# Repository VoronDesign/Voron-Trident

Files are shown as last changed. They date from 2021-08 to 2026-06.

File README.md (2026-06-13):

# Voron Trident
**[CLICK HERE TO DOWNLOAD](https://voron.zip/done/VT.zip)**

The above link includes the stealthburner toolhead files which are compatible with several of the printers in the Voron lineup. 
To keep things organized, StealthBurner’s files are maintained separately. 
the Stealthburner Repository can be browsed by clicking [HERE](https://github.com/VoronDesign/Voron-Stealthburner)

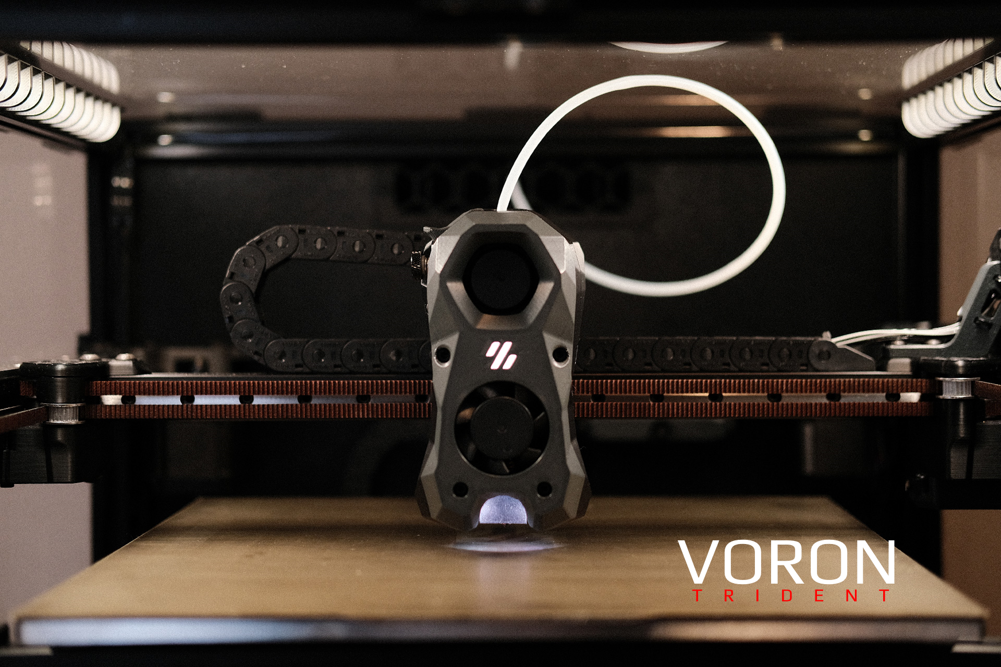
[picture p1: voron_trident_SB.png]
Image of Voron Trident


The official release of the Voron Trident 3D printer.  You can find the Bill of Materials in the configurator located at the [Voron Design]( http://vorondesign.com/voron_trident) web site.  The recommended sizes for this printer are 250x250x250, 300x300x250 and 350x350x250.

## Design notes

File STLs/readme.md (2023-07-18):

you can download the entire STL folder by clicking **[HERE](https://download-directory.github.io/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)**

This printer uses the StealthBurner toolhead, which is compatible with several of the printers in the Voron lineup. 
To keep things organized, StealthBurner’s files are maintained separately. 
the Stealthburner STL's can be downloaded by clicking **[HERE](https://download-directory.github.io/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)**

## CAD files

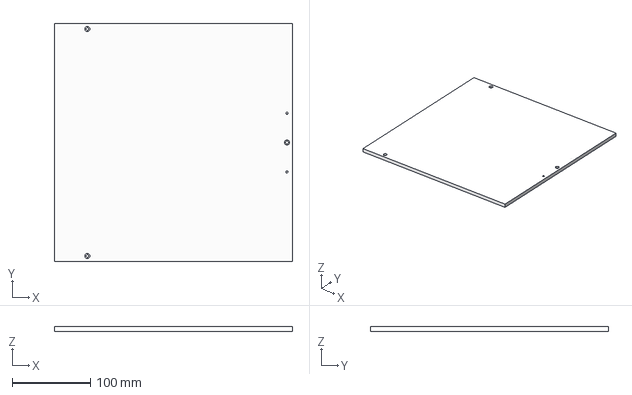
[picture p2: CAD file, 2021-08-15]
Drawings_DXFs/Build_Plate/MIC6_Bed_300.step
304.0 x 304.0 x 6.35 mm

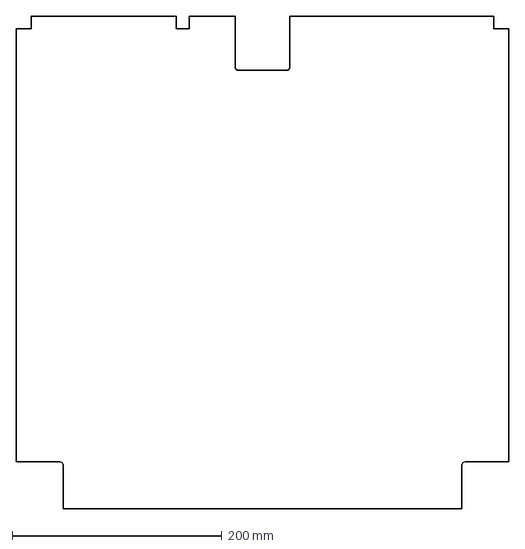
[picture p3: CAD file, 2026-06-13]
Drawings_DXFs/Panels/350_deck.dxf
469.0 x 469.0 mm

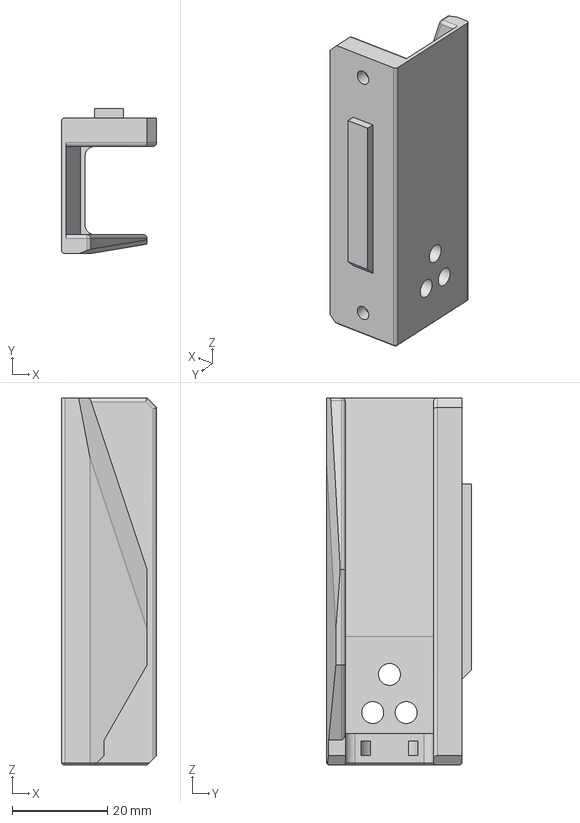
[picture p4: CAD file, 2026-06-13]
experimental/horiz_chain_umb/umbilical_mount_bottom.step
20.0 x 30.5 x 77.0 mm

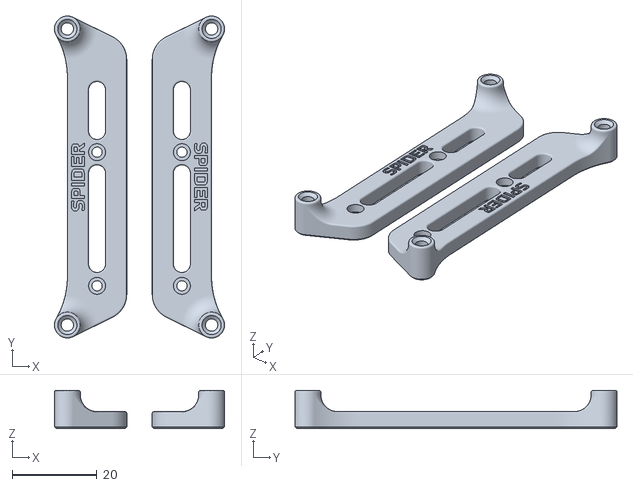
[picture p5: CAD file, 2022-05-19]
STLs/electronics_bay/controller_mounts/Spider_bracket_set.stl
40.1 x 75.9 x 9.00

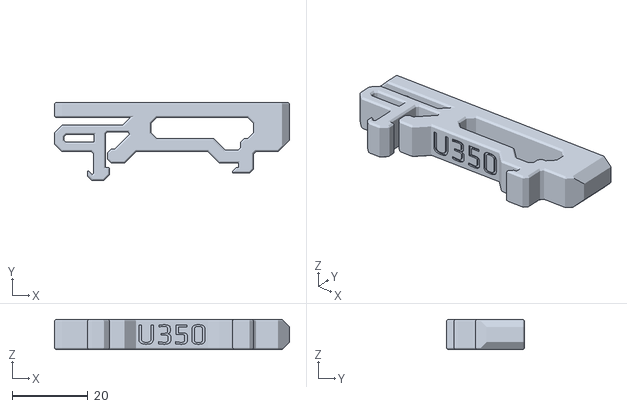
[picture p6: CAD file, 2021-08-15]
STLs/electronics_bay/other_ps_mounts/UHP_350_Mount_x2.stl
62.0 x 20.6 x 8.00

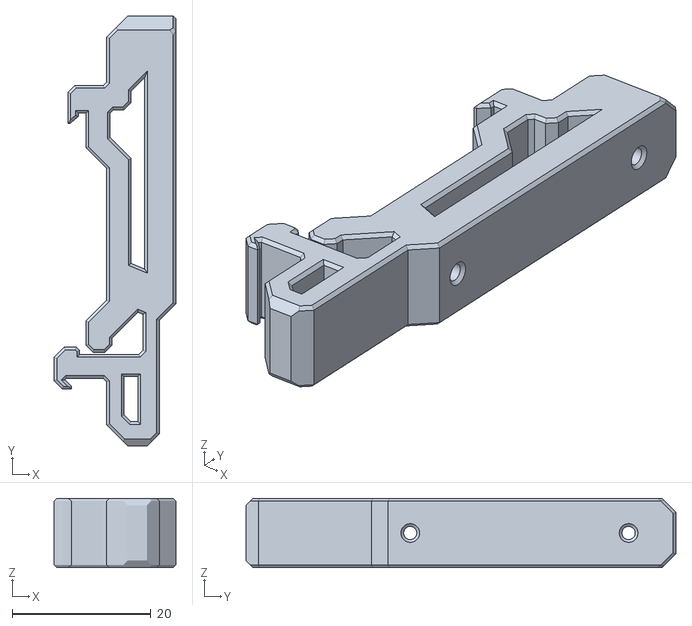
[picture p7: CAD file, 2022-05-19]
STLs/electronics_bay/pcb_din_clip_x3.stl
17.6 x 62.0 x 10.0

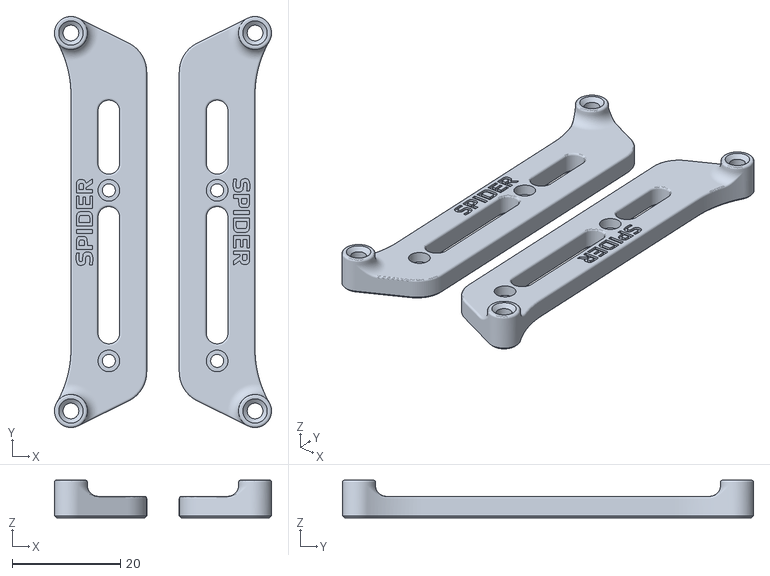
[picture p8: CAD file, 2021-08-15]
STLs/ElectronicsBay/Controller_Mounts/Spider_bracket_x2.stl
40.1 x 75.9 x 7.00

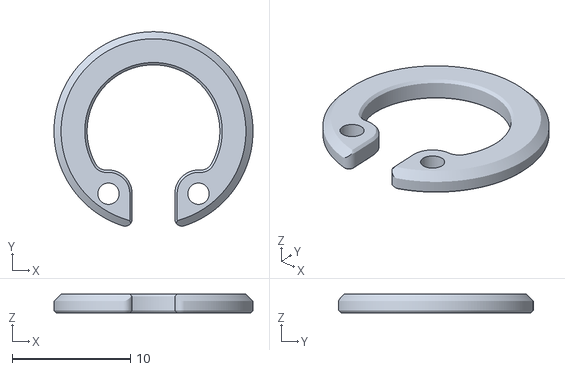
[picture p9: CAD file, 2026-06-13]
STLs/Gantry/ba_drive_units/circlip_x2.stl
16.8 x 16.4 x 1.60

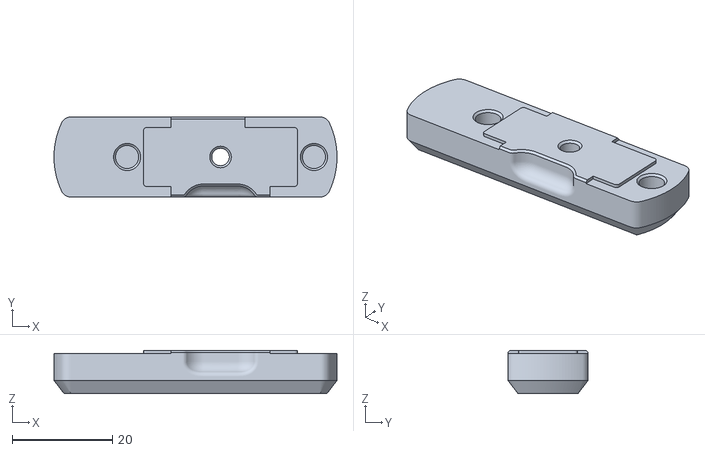
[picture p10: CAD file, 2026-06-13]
STLs/Gantry/Front_Idlers/[a]_idler_front_x2.stl
56.5 x 16.0 x 8.60

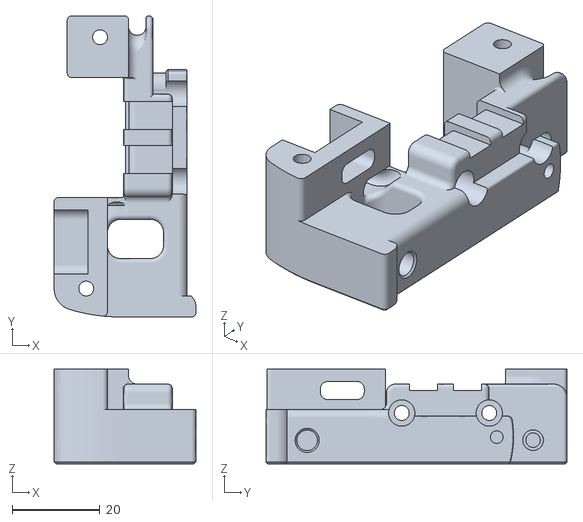
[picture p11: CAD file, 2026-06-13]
STLs/Gantry/X_Axis/X_Carriage/x_carriage_frame_right.stl
32.4 x 68.8 x 21.6

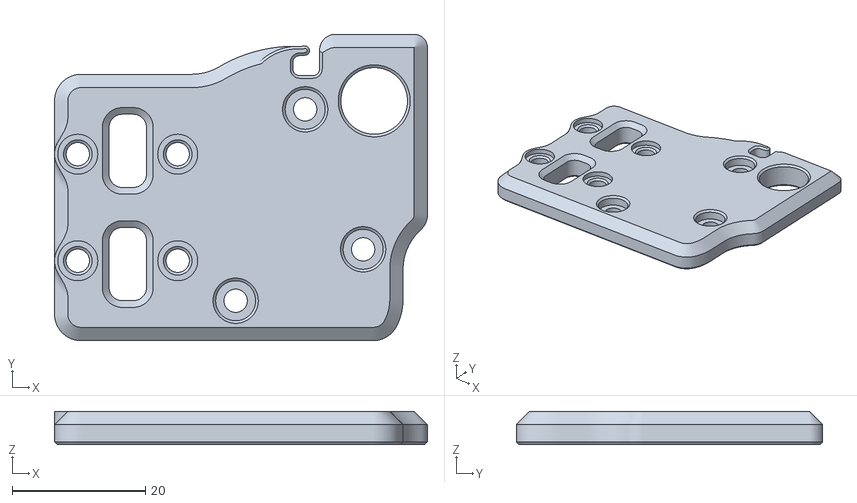
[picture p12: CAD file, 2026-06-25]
STLs/Gantry/X_Axis/XY_Joints/[a]_xy_right.stl
56.0 x 46.0 x 5.00

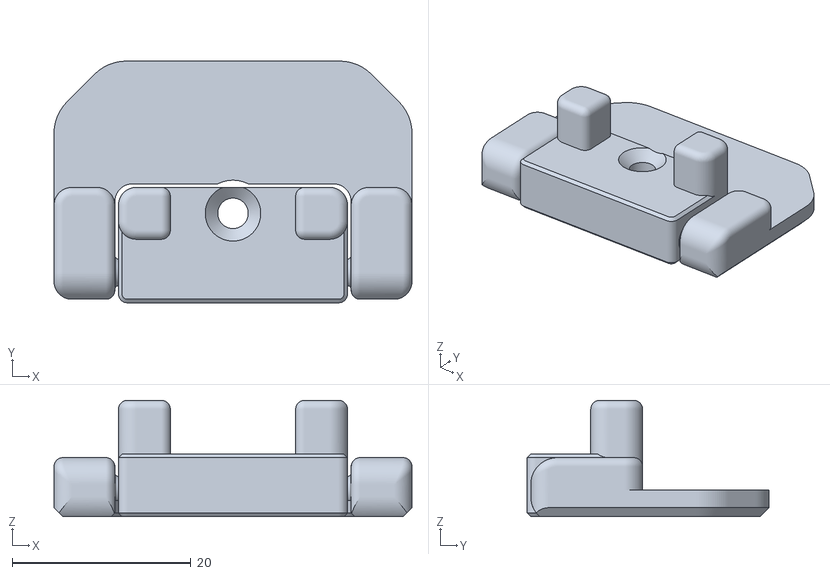
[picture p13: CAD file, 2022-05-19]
STLs/Panels/Front_Doors/door_hinge_x6.stl
40.0 x 27.0 x 13.0

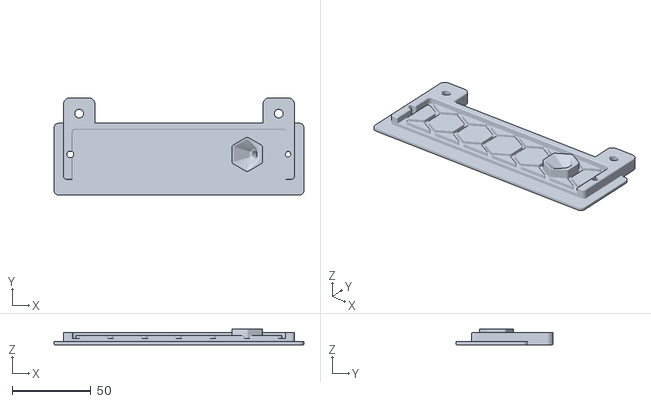
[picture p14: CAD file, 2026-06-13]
STLs/Panels/ptfe_rear_plate/ptfe_plate.stl
158.4 x 61.6 x 10.00

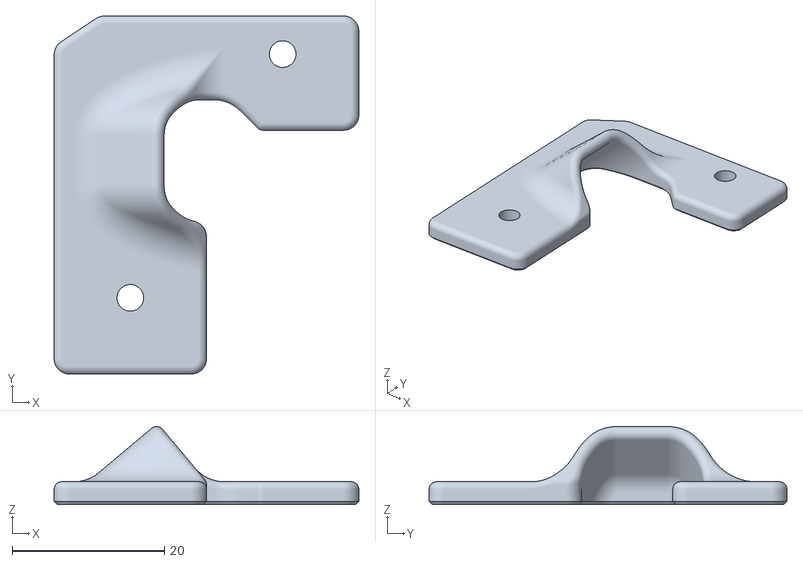
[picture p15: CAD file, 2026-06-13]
STLs/Panels/wire_cover_right.stl
40.0 x 47.0 x 10.2

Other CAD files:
STLs/Skirt/250/rear_skirt_center_250.stl
STLs/Skirt/300/front_skirt_left_300.stl
STLs/Skirt/350/front_skirt_right_350.stl
STLs/Skirt/rear_skirt_keystone.stl
CAD/native_assemblies/110mm_y_alignment_spacer.f3d
CAD/native_assemblies/[a]_z_stop.f3d
CAD/native_assemblies/ba_pulley_align_Tool.f3d
CAD/native_assemblies/deck_wire_covers.f3d
CAD/native_assemblies/front_idler.f3d
CAD/native_assemblies/ptfe_holder.f3d
CAD/native_assemblies/ptfe_plate.f3d
CAD/native_assemblies/rear_vertext_upper_brace.f3d
CAD/native_assemblies/spool_holder_base.f3d
CAD/native_assemblies/z_chain_lower.f3d
CAD/native_assemblies/z_mount_rear.f3d
CAD/native_assemblies/z_mounts_front.f3d
Drawings_DXFs/Build_Plate/MIC6_Bed_250.step
Drawings_DXFs/Build_Plate/MIC6_Bed_350.step
Drawings_DXFs/Panels/250_bottom.dxf
Drawings_DXFs/Panels/250_deck.dxf
Drawings_DXFs/Panels/250_rear.dxf
Drawings_DXFs/Panels/300_bottom.dxf
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

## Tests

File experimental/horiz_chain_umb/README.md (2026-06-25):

# Horizontal Chain Umbilical

## Components

**Corner PTFE Plate:** Alternative filament inlet path for the rear right corner (when viewed from the front). Requires a cutout in the back panel at that corner.

**Umbilical Mount (Bottom):** Attaches to the rear top horizontal extrusion from below. Available in 2- and 3-hole variants to suit different chain mount patterns.

**Umbilical Mount (Front):** Attaches to the rear top horizontal extrusion from the front. Available in 2- and 3-hole variants to suit different chain mount patterns.

## Images

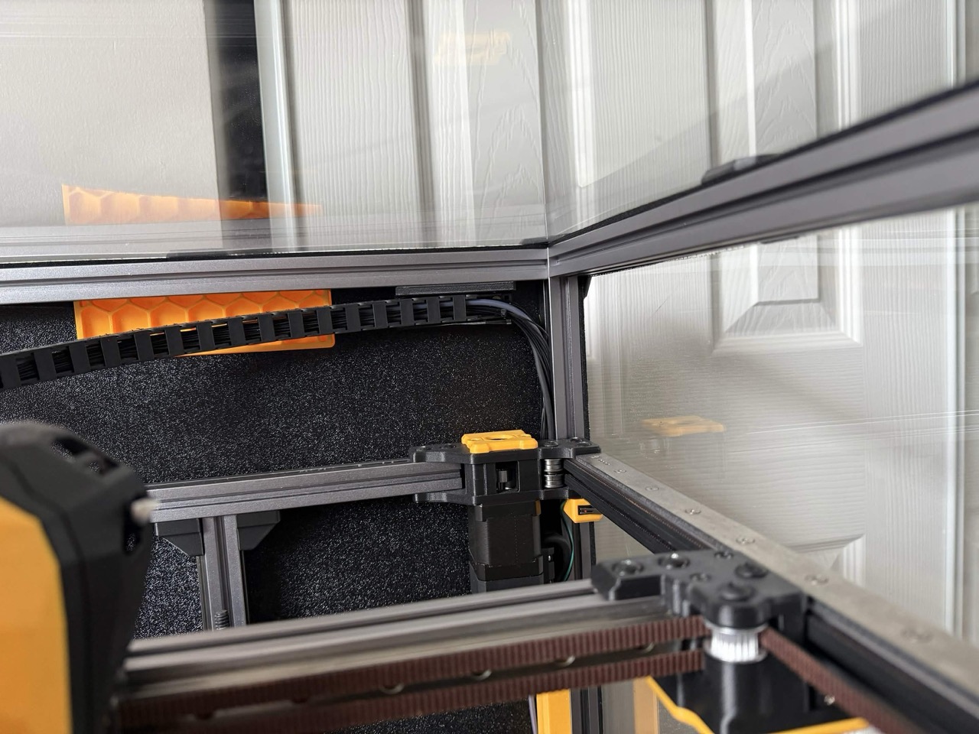
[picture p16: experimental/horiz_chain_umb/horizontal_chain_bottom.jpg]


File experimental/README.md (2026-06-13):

This folder contains parts that are not quite ready for release but we are excited to see tested.

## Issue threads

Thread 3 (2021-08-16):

Corrections for manual

koonweee, 2021-08-16:
This issue can be used to track all neccessary corrections to the manual.
Please add any corrections as a new comment :-)
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
^ contributed by Vapour3D Samuel#5741

mhoush, 2021-08-16:
On page 16 there's a label that says "PEPARE 8 EXTRUSIONS" rather than "prepare".

Yeriwyn, 2021-08-16:
Page 44, is there any way to highlight the m3, because with the m5 everywhere it’s easy to miss, and 3 and 5 do look similar

DunarDolorgiet, 2021-08-16:
Feel free to add annotation to https://assets.adobe.com/id/urn:aaid:sc:US:0f574b90-97b2-4771-a208-91fdc6357ab5?view=published

mhoush, 2021-08-16:
Transferred comments over there, cheers!

Closed 2021-08-30.

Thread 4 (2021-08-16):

Missing Value for BOM (M3 T-nut) in Configurator

Vapour3D-Samuel, 2021-08-16:
Missing Value for BOM (M3 T-nut) in Configurator

The BOM in the Configurator shows NaN for the M3 T-nuts

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

stvptrsn, 2021-08-16:
Thanks for the report.  We are aware that the configurator is not accurate right now.  Although if you have the link you can view it, the page isn't yet published.  We're working on it and will post an announcement on Discord when it is live.

Vapour3D-Samuel, 2021-08-16:
Great, thank you guys again!

DunarDolorgiet, 2021-08-16:
Fixed

Closed 2021-08-16.

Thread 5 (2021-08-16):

Electronics Bay File Naming Convention

Annex-Engineering, 2021-08-16:
Seems as if the electronics bay brackets use a different naming convention to the standard file structure, as when compared to the rest of the repo. Maybe remove the 2pc part, or something?

This may cause confusion to end users, especially legacy ones

Congrats on your release!
 - Trails

FHeilmann, 2021-08-16:
They're named "2pc" because the STL contains both parts of the mount, so the names are, in fact, correct.

-FH

Annex-Engineering, 2021-08-16:
I get that, just stating that it may be worth a comment in the file naming convention if your going to adopt this as a standard to prevent confusion with end users,

x# = print quantity
#pc = multiple parts in same file, etc

FHeilmann, 2021-08-16:
We'll keep it in mind if it comes up in the future.

Thanks for bringing it up

-FH

Closed 2021-08-16.

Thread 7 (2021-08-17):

Corrections for configurator generated BOM

koonweee, 2021-08-17:
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
Fork crimp terminals are not included

Kosh42, 2021-08-22:
Also, no M3 nylon lock nuts specified but they are called for on P78.

BerzerkaDurk, 2022-05-29:
>

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

nemgrea, 2022-10-11:
> 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 Fork crimp terminals are not included

how many for terminals are needed?

nemgrea, 2023-03-01:
no response

Closed 2023-03-01.

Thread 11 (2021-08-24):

X Carriage Frame, Belt Bolts conflicting with extruder asembly.

MadsGadeberg, 2021-08-24:
Hi Voron Team.

It seems that the bolt head is only recessed by 2,2mm.
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

SHCS M3 bolts require 3mm to be flush installed.
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

The Extruder assembly is the Galileo type but the backplate should be the same on where the issue is.

eddietheengineer, 2021-08-24:
Thanks for letting us know! The Clockwork motor plate has clearances for the screwheads so they don't intersect:

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

Galileo STLs generally aren't included with the stock Voron releases, so you will likely have to add a similar feature to the Galileo parts.

MadsGadeberg, 2021-08-24:
Fuck me Eddie. Ty for the update end sorry for the sloppy issue.

A ton of ty for these projects by the way! i respect that!

eddietheengineer, 2021-08-24:
If you can open the CAD--it's always possible that the Galileo CAD with a tweaked motor plate is in the assembly (maybe hidden). I'm not positive but it might be there!

MadsGadeberg, 2021-08-24:
Ill check and leave the result in the comments for others to see.

MadsGadeberg, 2021-08-24:
I used an early version of the Galileo Extruder which didnt have the groves shown on the picture.
Feel free to close the issue and many ty for help!
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

Closed 2021-08-24.

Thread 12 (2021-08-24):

Proble and nozzle clearance to small

MadsGadeberg, 2021-08-24:
Hi Voron Team.

I have assembled the Trident MGN12 assembly on my 2.4.

The clearance between the Probe and nozzle is causing me issues. I looked in both the Afterburner CAD and the Trident CAD to se the difference. Here is what i found:

The new MGN12 leaves 1mm of clearance:
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

The Old Afterburner leaves around 3mm of clearance:
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

My build:
The probe is a bit deformed by the heat but the left and back part shows the original shape. I could maby install the probe a tiny bit higher but it does not solve my problem.
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

It seems that the clearance of 1mm is a bit to small to account for assembly tollerances.

eddietheengineer, 2021-08-24:
Yes--this is one of the tradeoffs for the MGN12 axis, you need a different probe as shown here:

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

The PL-08 was likely kept in CAD as a reference to show that it wasn't practical to use

stvptrsn, 2021-08-25:
Technically, the PL08 _should_ work if you have a Mosquito hotend.  But it's easier to recommend moving away from the PL series.

MadsGadeberg, 2021-08-25:
I have pushed the PL up as far as i can and it is just enough. I reckon i have below 0,5mm of clearance which is above 0.

Closed 2021-08-25.

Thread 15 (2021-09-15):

Wrong extrusion referenced on pg 132

billyclaymyersmsft, 2021-09-15:
Pg 132 incorrectly calls out H Extrusion for a second time, with this time being part of the bed frame. This should be G Extrusion.

H is called out correctly on pg 18, and pg 12 indicates there should only be 1 H. Since H is 330mm and the only extrusion whose side remains constant regardless of X,Y dimensions the pg 18 reference must be correct making the pg 132 reference incorrect.

billyclaymyersmsft, 2021-09-15:
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

Closed 2021-12-15.

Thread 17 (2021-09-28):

X Carriage Hex Hole Rounded

crashmaxx, 2021-09-28:
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

I noticed the bottom hex nut hole has a round cut going into it some depth.

Since all the other carriages have plain hex holes for the nuts, I'm guessing this is an error. It's an easy fix and I don't mind putting in a pull request, but I wanted to check if someone might have intentionally made it that way first.

The same also applies to the V2.4 MGN12 mod.
[https://github.com/VoronDesign/VoronUsers/tree/master/printer_mods/arkeet/mgn12](url)

bdbell, 2021-09-28:
The rounded area is to allow for the insertion of a 6x3 magnet to use with the Hall effect end stops.

crashmaxx, 2021-09-29:
> The rounded area is to allow for the insertion of a 6x3 magnet to use with the Hall effect end stops.

I didn't realize that. No problem, I'll close this.

Closed 2021-09-29.

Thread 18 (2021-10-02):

Looks like the Assembly Manual file has an issue

BernardG, 2021-10-02:
When trying to download "https://github.com/VoronDesign/Voron-Trident/blob/main/Manual/Assembly_Manual_Trident.pdf" through a browser, I get an error "something went wrong".

The message is a little less cryptic with Adobe Acrobat Reader :
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

No problem at all with the other PDF "Frame Upgrade Trident"

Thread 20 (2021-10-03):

Panel DXFs seem to have a units issue.

BerzerkaDurk, 2021-10-03:
When I open the any of the files in Drawings_DXFs/Panels, they load with the units seemingly scaled incorrectly by a factor of 25.4:1.

For example, the Trident 350 back panel opens with a width of 12,166.6 mm. If I then change the units to inches, I get the correct mm values, but with the wrong units. For example, the above becomes 479 inches.

This happens in both SolidWorks and eDrawings Pro. The 2.4 DXFs open just fine.

silence48, 2022-07-11:
You need to change the units to millimeters when you import the file.  There is 25.4 mm in 1 inch. Your software is thinking 1 mm is 1 inch, thus it is scaled 25.4:1

BerzerkaDurk, 2022-07-11:
Nice of you to assume I'm an idiot. I see you neither read my post nor tried it for yourself.

BerzerkaDurk, 2022-07-15:
The panel DXFs open fine in Fusion 360. I'm assuming there is some odd bug when trying to import them into SolidWorks.

Accordingly, I'm going to close this issue.

Closed 2022-07-15.

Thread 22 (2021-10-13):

M5 bolts on XY joints are chamfered instead of bridged

henrikssn, 2021-10-13:
This is originally for the V2, but it was suggested in the engineering ticket on Discord to submit the issue for Trident since it has the most recent gantry.

Issue: The recess for the M5x40 BHCS bolts in the XY joints are chamfered. This causes the bolts to slowly creep for me, which means I continuously need to re-tighten them

Fix: I used the "bridging trick" which resolved the creeping.

I'm happy to contribute my fix if possible.

timmit99, 2021-10-13:
Chambered? Do you mean chamfered?

henrikssn, 2021-10-13:
> Chambered? Do you mean chamfered?

Correct, I fixed the title/description (sorry, I'm not a native speaker)

BerzerkaDurk, 2022-05-22:
I believe this was addressed in the R1 update

stvptrsn, 2022-05-23:
Yep, I must have forgotten to link the issue.  Thanks!

BerzerkaDurk, 2022-05-23:
You betcha. Great job with the update.

james5843, 2022-05-28:
For anyone who doesn't know what the cross bridge method it like I did, [this video](https://www.youtube.com/watch?v=W8FbHTcB05w) outlines it in detail. A cool design technique!

Closed 2022-05-23.

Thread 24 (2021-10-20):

Include warning about needing a BAT85 diode for the inductive probe depending on control board

ShawnBuckley, 2021-10-20:
The sourcing guide notes that a BAT85 diode and 6+ stepper board is required while the assembly guide uses the Fysetc Spider specifically.  The assembly guide has the probe directly connected to the Z+ port on the Spider without BAT85 diode. Some users might be unaware that the Spider has a BAT85 diode built in and connect the probe without diode to a board which does not support that. Including a note in the assembly should give users a heads up to be aware of what their configuration is and if they need to include the diode or not.

Closed 2022-05-19.

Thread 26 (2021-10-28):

MGN 12 trident.

selimayaz, 2021-10-28:
Hello not an issue but i wonder anyone made or have MGN12 design for this printer?

stvptrsn, 2021-11-01:
Hi @selimayaz your best chance for any information on modifying the design will be at the Voron Discord.  MGN12 for the Y and Z rails poses a problem in that the MGN12 cartridges are wider than the 2020 frame extrusions so would rub on the enclosure panels.

Closed 2021-11-01.

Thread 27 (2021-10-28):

Possible confusion on Page 19/20 when not using a 250mm frame size

wattsie, 2021-10-28:
Hi all,
  Just a quick note about using the "E-Extrusion" for setting the height of the "A-Extrusions" (on Page 19/20).
  It only works when using the 250mm frame size... (I am building a 350mm frame size Trident)

  If the height needs to be exactly equal, maybe the process should change to construct the the left and right "A-Frames" (B+A+A+B) by two, using the "H-Extrusion" as the height guide.
  Then joining these two "A-Frames" with the front and back (H+C) and (A) Extrusions to give you the full base.
  Then no matter the frame size, as the "H-Extrusion" is common and 330mm in all designs, it works.

  Does that make sense?

  Being that the one manual is being used for the three primary designs, it actually only works for the 250mm frame size.
- 250mm frame's E-Extrusion is 330mm
- 300mm frame's E-Extrusion is 380mm
- 350mm frame's E-Extrusion is 430mm

So, maybe, on Page 19/20, put a note say the E-Extrusion can only be used on a 250mm frame size, all others require the printed spacer or manual measure.

Many thanks.

Cheers.

Closed 2021-12-15.

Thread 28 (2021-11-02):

The Frame upgrade guide should list extrusion lengths for 300 and 350 frames.

bwattendorf, 2021-11-02:
I have found it hard to cross reference the right lengths to convert a 1.8 frame to a Trident frame for a 300mm printer. I also suggest that the Trident letter frame be added to the Sourcing guide for each extrusion.

BerzerkaDurk, 2021-11-05:
Couple points:
1. there are no standard 350 mm 1.8 frames.
2. a. Only the Z, rear, bed rear, bed front, and rear bottom extrusions are modified.
    b. The Z extrusions are the same regardless of build size.
    c. For the bed front and bottom rear extrusions, center is center regardless of build size.
    d. For the bed rear extrusion, it is cut 138mm from the end regardless of build size.
    e. For the rear extrusion, it is 330mm long regardless of build size.

agentk, 2022-10-18:
I struggled with the lengths of extrusions from a Format 350 kit and used the wrong length for H Extrusion first time. I ended up making myself a reference for the extrusions in a 350x350x250 kit. (I might have messed something up but you get the idea)

- A Extrusion: HFSB5-2020-500-LCP-RCP-AV360
- B Extrusion: HFSB5-2020-470-TPW
- C Extrusion: HFSB5-2020-470-AH235-TPW
- D Extrusion: HFSB5-2020-340
- E Extrusion: HFSB5-2020-430
- F Extrusion: HFSB5-2020-470-AH235
- G Extrusion: HFSB5-2020-332-LTP
- H Extrusion: HFSB5-2020-330-LTP

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

BerzerkaDurk, 2022-10-18:
Yeah. You definitely have the A and B extrusions mixed up on both your chart and picture. This issue was specifically raised for the upgrade guide, so you should probably create a separate issue for this, if you want. I was sure that they'd listed the extrusion letters for each size in the sourcing guide, but i must've dreamt it.

Tuxedo-VE, 2023-04-03:
Actually I think agentK has it exactly right. The BOM and the manual both specify 4 B extrusions ( which have 3 sets of screw head access holes but no threading on the ends) and 9 A extrusions (which have no screw access holes but are threaded on both ends) + 1 C extrusion (which are the same as the A extrusions but with a hole in the middle). The B extrusions form the 4 main uprights of the frame while the A and C extrusions form all the fixed horizontal pieces of the frame. Trust me I spent hours unravelling all this so I know.

IMHO the Trident assembly manual is badly in need of a graphic similar to the one he made in his post. It would have saved me and a lot of other first time builders a ton of time.

itsgudenuf, 2023-08-22:
Just wanted to say thanks to @agentk, that image was worth a thousand words. I was struggling to figure out the various extrusions after opening my Fysetc "kit". After finding this issue, it was a snap to identify them all.

wa2mze, 2025-07-23:
I have a v1.8 300mm frame kit.  This is a 250mm high (Z) size.  I will have to cut some of the extra 420mm extrusions from the v1.8 down to size for the 282 and 330 size extrusions, the 1.8 frame has a 380mm already.  The 330mm  H extrusions can be used as a spacer when mounting the side C extrusions, if it is mounted last.  The E extrusion is a different length than the one on the 250 size trident.   The diagram shown above is for the 350 size trident, the extrusions letters are correct.

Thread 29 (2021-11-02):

Assembly and frame upgrade manual needs extrusion access hole drill size.

bwattendorf, 2021-11-02:
In the assembly manual and the upgrade manual there is no mention to the drill size for the access holes that need to be drilled in the extrusion.

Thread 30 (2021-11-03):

Broken hyperlinks within the Assembly Manual

simonrwatts, 2021-11-03:
1) Link on page 121 doesn't work due to a space in the text of the link after link/

2) On page 248 of the Assembly Manual one of the links is broken. https://voron.link/m6wtwnl

It's in this text on the page:
If you are using a “FYSETC mini12864” please review section 3.3 of the FYSETC Spider documentation (https://voron.link/m6wtwnl).

Note: I just did a search for voron.link within the PDF and tested all the links, the rest are currently working.

BerzerkaDurk, 2021-11-26:
Weird. It works for me.

Closed 2021-12-15.

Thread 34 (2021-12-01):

Manual (page 53) needs to point out offset of vertical extrusion

mikem1017, 2021-12-01:
As a first time voron builder, I found this page to not be clear enough that the vertical extrusion will then be offset from the horizontal extrusion, and in which way (in or out) from the extrusion.  After some questions on the discord, I have found that other folks believe this to not be 100% clear either.

Thus I would like to propose a "red circle" around the corner piece highlighting the outward (way from the print bed) offset of the vertical extrusion relative to the horizontal extrusion.

jarrettv, 2021-12-01:
I've seen this asked multiple times over the past few months in discord. So include the answer in the manual as well: the offset is for the belts which are routed behind the extrusion

Closed 2022-02-12.

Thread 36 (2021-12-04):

Manual page 16 "PREPARE 8 EXTRUSIONS" seems incorrect

DanTup, 2021-12-04:
On page 16 it says:

> PREPARE 8 EXTRUSIONS
> 8 of the 9 extrusions are going to be used in this section. Prepare them as shown above.

However this doesn't seem correct to me. Assuming it is referring only to A Extrusions, there are 9 of them, but as far as I can tell all 9 need preparing in the same way:

- 3 initially used for the base (with a C extrusion being used for the back)
- 2 used for Y
- 4 remaining ones used for the top

All of them seem to be prepared with screws in each end. It's not clear to me why it says "8 of 9".

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

Closed 2021-12-15.

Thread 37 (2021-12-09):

Recommended Filtered Power Inlet TE 10EGG1-2 requires two fuses, while BOM only lists one.

leanghoun, 2021-12-09:
Recommended Filtered Power Inlet TE 10EGG1-2 requires two fuses, while the BOM only lists one. Additionally, NA code prohibits fusing of neutral.

nemgrea, 2022-10-11:
bom change request submitted

Closed 2022-10-11.

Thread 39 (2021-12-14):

Trident assembly manual is low contrast, hard to read

mapsedge, 2021-12-14:
The text in the Trident assembly manual is gray, and extremely hard to read for those of us with diminishing eyesight. I know gray is fashionable and "cool", but black on white is easier to read, and ADA compliant.

FHeilmann, 2021-12-15:
Thanks for bringing this to our attention, we'll forward this to the documentation team for consideration. In the meantime I want to humbly suggest you make use of the High Contrast mode included in Adobe's PDF readers to help with this issue.

-Florian

ptyork, 2022-01-19:
Came here to make this very report. Amazed to find someone else had already reported it. It truly is hard to read both with a white background. And it doesn't work at all inverted (which is how I need to read it). The "high contrast" modes in Adobe Reader (and FoxIt and Xodo) do nothing to help with the contrast for these documents. Not sure why. The font is also tiny and thin, all things incompatible with low vision.

I know this is far from a common issue. Perhaps you could simply make the source files (docx??) available on GitHub, those of us with these issues may be able to help ourselves by like Ctrl+A and change the color.

tknapstad, 2022-02-24:
I completely agree. This is an assembly manual, low contrast colors have no place here.

Those who are not on Linux like me can use Adobe Reader to change colors. "Preferences -> Accessibility -> Replace Document Colors + Custom Color" will let you set it to white/black or black/white.

I would also like the source document to be published on Github. A .docx or whatever is something I can open and edit under Linux as well, and it's much easier to annotate to add personal notes than a PDF.

tknapstad, 2022-02-25:
> Those who are not on Linux like me can use Adobe Reader to change colors. "Preferences -> Accessibility -> Replace Document Colors + Custom Color" will let you set it to white/black or black/white.

I tried this on a Windows laptop and it didn't work either, so this needs to be fixed at the source. None of the accessibility tools in Adobe Reader, Foxit Reader or Okular are able to modify the font colors of this document.

DunarDolorgiet, 2022-02-25:
Please have a look and see if **https://github.com/VoronDesign/Voron-2/blob/Voron2.4/Manual/Assembly_Manual_2.4r2_highcontrast.pdf** addresses your needs. If it does, I can include this styling in the next update of the document.

As for accessibility options in Adobe Reader, I'm using the following settings which appear to work fine on my end:
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

ptyork, 2022-02-26:
> Please have a look and see if **https://github.com/VoronDesign/Voron-2/blob/Voron2.4/Manual/Assembly_Manual_2.4r2_highcontrast.pdf** addresses your needs. If it does, I can include this styling in the next update of the document.

Thanks, yes, that is much, much better.

> As for accessibility options in Adobe Reader, I'm using the following settings which appear to work fine on my end: 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

Yeah, depends on the PDF viewer, platform and needs. I need inverted text. Adobe Reader doesn't do a very good job with inverting images. And by not good job, I mean you can't see the images in the manual.

I do have better luck with 3rd party readers sometimes. Found one (Xodo) that can work for most pages on the PC. Still looking for a good one on my iPad, though.

I DO however see the high-contrast (non-inverted) options ARE in fact working for me in Acrobat DC (paid) but were NOT working in Acrobat Reader DC (free). Perhaps this is the reason for the discrepancies in what we are reporting?

Regardless, if you can switch to the high-contrast version above (or offer it as an option) that would be fantastic.

Thanks a lot!!

atoomnetmarc, 2023-09-30:
It would be awesome if the high contrast manual returned.

I saw it here: https://github.com/VoronDesign/Voron-Trident/tree/b87f1adac669c8e8c0e9c21d428924088ad0a51a/Manual

It was deleted in this commit: https://github.com/VoronDesign/Voron-Trident/commit/79750725c457ceb16260322cf83922eb3b04ed33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

Closed 2022-05-19.

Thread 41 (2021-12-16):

Voron Manual has live and neutral reversed on 5v PSU

PhoenixMage, 2021-12-16:
Page 209 of the manual has the neutral and live wire reversed on the PSU. Live should be pin 1 and neutral pin2.

My understanding is this has no negative consequences but it doesnt match watch is printed on the PSU itself and should be fixed for clarity.

Closed 2022-02-12.

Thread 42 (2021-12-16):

Make bed heater and magnet placement more obvious

Lycowolf, 2021-12-16:
Hi,

on pages 127 - 128, there's no clear indication to which side of the bed the heater and magnet should be attached. When comparing the diagrams, I can see the holes under the magnets to be slightly larger, indicating a countersink (the hole for the screw head: I hope this is the correct term), and the holes under the heater slightly smaller, but nothing points out the distinction, and the diagrams are on separate pages, making the comparison hard.

The issue is made worse by the fact that both the magnet and the heater are glued to the bed, making fixing an eventual mistake impossible without damaging both, or devising a workaround. (Guess how I found out. Even after discovering my mistake and rechecking the manual, I can see myself doing the same mistake again: it really isn't clear.)

I would recommend adding a cutout showing a hole profile and both the heater and the bed clearly marked, including the blue circle used to point out important details.

Closed 2022-02-12.

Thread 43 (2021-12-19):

Squaring instructions note to move the gantry to A and B drives to square.  B drive has protruding Y endstop bracket.

mobilemcclintic, 2021-12-19:
In the manual on page 118, we are instructed to move the gantry back to the A/B drives to square the gantry.  The gantry hits the Y endstop block before hitting the A/B drives.  This makes the travel on the right side shorter than the left and had me wondering how in the world I could rack the gantry but always have the left side not be the one stopping.

mobilemcclintic, 2021-12-19:
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

j-heffron, 2023-08-05:
The change in the assembly manual noting to rack the gantry to the front idlers rather than the AB drive motor assemblies appears to have been reverted by #68. As far as I can tell, there has not been any change to the y endstop bumper part to warrant reverting the instructions.

Closed 2022-02-12.

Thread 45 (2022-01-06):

Hot / Neutral Wires reversed on power inlet diagram, page 208

BerzerkaDurk, 2022-01-06:
Hate to post this in multiple places ( I put it in an engineering ticket on Discord, as well ), but this seemed important.

on page 208 of the Trident Assembly Manual, it shows the neutral on the left, and the hot on the right, when the ground lug is down:

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

these should be reversed, as shown on the inlet diagram itself:

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

this may not be 100% necessary in countries with reversible outlet plugs, but in North America, it's mandatory to comply with the National Electrical Code.

I looked at the manuals for the other Voron models. Only the 2.4 uses the same inlet, and the colors are correctly called out in the 2.4 manual.

edit: spelling

Closed 2022-02-12.

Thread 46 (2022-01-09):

XY End-Stop Pod wiring length

etjensen, 2022-01-09:
The manual p.203 suggests 150mm of wire for the end stop switches. Not. clear what is intended for where this length is supposed to get you. It would be better to leave the XY end stop pod wiring until later when the Y drag chain is in place so the wire length can be measured out (or give actual wire lengths for the standard builds.

raymondh2, 2022-01-09:
This is so you can add a connector to the spec stand alone microswitches so you can disconnect them without unsoldering them

etjensen, 2022-01-09:
Cool- makes sense in retrospect. Adding a comment on p.203 that says "Later we will add connectors to these wires" or something would help. I ended up running long wires as it never occurred to me.

Closed 2022-01-09.

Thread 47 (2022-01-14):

Assembly manual pg. 273 BHCS

rlaferla, 2022-01-14:
The manual needs to indicate two M5x10 BHCS are used to attach the exhaust mount.  Also, two M5 t-nuts should be inserted in the extrusion for the screws.

Closed 2022-02-12.

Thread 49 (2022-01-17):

A list of suggestions for the manual from my Trident build

Sparohok1, 2022-01-17:
I just finished my build. I thought the manual was great, super clear, clearly a ton of work went into it. Still there were a few places I had notes or nitpicks.
p. 10/11/12 - little tables with lengths for each model would be helpful (or formulas e.g. "370 + D" where D is 0, 50, 100 for 250, 300, 350 builds)
p. 18 - 175 + D/2
P. 54 - 175 + D/2
p. 115 - will this procedure really make gantry square without removing hall endstop mount? for me that hits first! Edit: See also #43
p. 121 - a table of "typical" and "maximum" belt lengths for each frame size would be really useful. (for 300 build: https://discord.com/channels/460117602945990666/551488536256184331/926551021193408524)
p. 121 - mention correct tensioner position for this procedure (e.g. position tensioner in the ~middle of its range of motion~ minimum tension before measuring)
p. 127 - mention cutting holes for 3 screws in the magnet if not already die cut
p.130 - for me this was not a press fit. but heating up the ABS with heat gun made for easy fit
p.132 - ~Labelling of extrusions is wrong (https://discord.com/channels/460117602945990666/551488536256184331/918558358896775199)~ Edit: fixed in #15
p. 149 - mention which direction to install heater and thermistor (its implied on p152.., see https://discord.com/channels/460117602945990666/551488536256184331/926588851298906163)
p. 150 - chamfer ptfe tube?
p.157 - mention set screw on drive gear
p.199 - mention m4x6 screws for omron?
p.209 - N and L are reversed for RS-25-5 Edit: See also #41

I see that some of these are already filed as issues in the github, sorry about the duplicates but this is the list of what I saw in my build.

Sparohok1, 2022-01-17:
Let me know if there's anything I can clarify, or if you'd prefer individual issues for each item.
Also, in the spirit of an open source project, I'm happy to try fixing these myself but I don't see any source document for the manual, just PDF.

BerzerkaDurk, 2022-01-17:
p 115 - https://github.com/VoronDesign/Voron-Trident/issues/43
p 121 - belt length is in BoM
p 121 - no. install belts with the tensioners at their "min" positions. they aren't going to get shorter
p 132 - https://github.com/VoronDesign/Voron-Trident/issues/15 ( closed: already fixed )
p 199 - the screws for mine came with the DIN rail mount. is that atypical?
p 209 - https://github.com/VoronDesign/Voron-Trident/issues/41

Sparohok1, 2022-01-18:
@BerzerkaDurk Thanks! I edited accordingly.
p.121 The belt length in the BOM is much longer than my build. I think that's a good idea, better to order too much than too little, but it caused me some soul searching that my measurement was so far off. See the linked post/thread. A table of _typical_ values would be useful which doesn't seem to be what the BOM values are based off of. But I should hasten to add, like many of these comments I'm just listing things that confused me, I'm leaving it to more experienced to judge whether these are real problems!
FWIW I measured with tensioner at midpoint and it worked well for me. That way I avoided the temptation to "add some slack" and went with my exact measurement. I don't think these belts stretch much at all. But I don't really have a strong opinion on the actual recommendation, just that its something worth specifying one way or another for first time builders!
p.199 - My DIN mount didn't come with screws in the package, they were included in the kit however (Formbot). But if they normally come with the mount it makes sense why its not in the manual!

Sparohok1, 2022-01-18:
There are 7 M4x6 screws in the BOM. 4 on page 192, 1 on page 198, so I'm pretty sure the last 2 are for the Omron on page 199.

Closed 2022-02-12.

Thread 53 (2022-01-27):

Cannot Download the .STL files for A or B Drive Frame Lower - Both files appear to be corrupted.

Rwhite692, 2022-01-27:
When attempting to download the STL files for the A and B drive Frames (Only the Lowers), Clicking "Download" on either of these two files, results in no download initiated, just a display of a raw ASCII text file.
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

raymondh2, 2022-01-27:
STLs can be binary or ASCII. Right-click and save as

Rwhite692, 2022-01-27:
Thanks Raymond, I tried that, however these two .STLs will not open in Cura...returns an error message (File is either corrupt, or contains no model data). I even fired up F360 to see If I could import them, with no luck (Was thinking I could import as ASCII / Export them as Binary .stl) ....I am not well versed in dealing with ASCII .stl files so I'm kind of at a loss here...

Rwhite692, 2022-01-27:
Hi Raymond, FYI, I figured it out, and I should have occurred to me.... Windows was adding a hidden extra ".txt" extension after the ".stl" extension (creating filename.stl.txt, with the .txt being conveniently invisible). Newer laptop and never thought to check this. Best Regards, -Rob

Closed 2022-01-27.

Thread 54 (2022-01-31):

Manual does not specify where 1mm and 3mm tape and respective clips are used on panels.

BerzerkaDurk, 2022-01-31:
After the question coming up a couple times on Discord, I would like to humbly suggest that a label indicating the proper clip and correct thickness foam be added to pages 254, 256, 257, 259, and 261.

The rear and top panels (pgs 254 and 261) should indicate 1mm thick foam, corner_panel_clip_4mm, and midspan_panel_clip_4mm

The side panels (pgs 256, 257, and 259) should indicate 3mm thick foam tape, corner_panel_clip_6mm, and midspan_panel_clip_6mm

Closed 2022-02-12.

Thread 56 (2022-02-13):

SSR wiring on pg 115 inconsistent with updated switch wiring

BerzerkaDurk, 2022-02-13:
Thank you for updating the inlet, switch, and 5V PSU wiring.

The SSR wiring on page 115 just needs an update to be consistent with the updated wiring on pgs 210 and 211

Pages 210 and 211 - blue on left of switch:
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

Page 215 - blue on right of switch:
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

Closed 2022-05-19.

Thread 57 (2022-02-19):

Spider v2.2 interference with mount

poernahi, 2022-02-19:
The spider mount provided could not be fully secured to v2.2 board due to interference with fuse F7 under the terminal blocks.

poernahi, 2022-02-22:
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

stvptrsn, 2022-04-10:
Yep, that stupid fuse they added after the Spider v1.  THis will be fixed in the next Trident release.  In the meantime the V2.4r2 files has an updated mount.  Alternatively you can rotate the mount 180 degrees to clear the fuse.

Closed 2022-05-19.

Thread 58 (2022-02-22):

Clarify Hall Effect Magnet Installation Process

SkiBikePrint, 2022-02-22:
It would be helpful to call out the process for magnet installation for the hall effect sensor on pages 50 and 109.  Page 50 states "HALL EFFECT ENDSTOP? If you are using a Hall Effect Endstop board remove the highlighted part and insert a magnet in its place".  This infers that it should be done as part of prep but the Hall Effect endstop setup document on the Voron web site instructs to wait to install the magnets until the sensor can be powered up and correct magnet polarity determined.  I am not the first to install the magnets during the build in advance of being able to power and test the sensor.  If you get it wrong you pretty much need to reprint the endstop  and/or the x_carriage_frame_right parts.  Thanks, Glenn.

Macmagoo, 2022-03-04:
Unfortunately I did the same luckily I only have to print the endstop.

kodekill, 2022-03-13:
Luckily I didn't glue my magnets in early, but I did find the installation for the hall sensor confusing. I don't recall there being anything in the manual that refers to putting a magnet in the x cariage, just the breakout for the y direction.

nwalasek, 2022-03-14:
I also suffered this fate. Another secondary issue I ran into is the placement of the magnets - they don't line up with the point in space the sensor wants to trigger from.

BerzerkaDurk, 2022-05-22:
To clarify, the issue with the Y endstop is now on pg 48 of the latest manual. I don't see the X endstop magnet referred to anywhere, but at least that one can be pushed out through the screw hole on the opposite side, if it needs to be reversed.

Closed 2022-08-16.

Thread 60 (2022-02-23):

Mean Well LRS-200-24 Wiring Mismatch

samuraihelmet, 2022-02-23:
Per the Mean Well datasheet linked in the manual [here](https://www.meanwell-web.com/content/files/pdfs/productPdfs/MW/LRS-200/LRS-200-spec.pdf) and the labeling on the part itself, the pin labeling and wiring shown on pages 211 and 216 is incorrect. The manual shows L/N/G in terminals 9, 8, and 7, while the spec sheet places them in 1, 2, and 3. Similarly, +V and -V are flipped on the output terminals.

Closed 2022-05-19.

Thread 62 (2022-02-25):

Wrong position of heat set insert hole on front_skirt_b_350

Promix953, 2022-02-25:
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

stvptrsn, 2022-04-10:
Thanks for the report.  I'll include it in the next release.   The problem is opposite of what you expect though.  It's actually side A that's wrong :)

Closed 2022-05-19.

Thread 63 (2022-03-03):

Misspelling in Assembly Manual

blite, 2022-03-03:
Page 17 "MIND ACCESS HOLE POSITION" -> "BLIND ACCESS HOLE POSITION"

blite, 2022-03-03:
I guess this is technically okay as is, just seems odd on first read.

blite, 2022-03-04:
I think we should close this unless someone else brings it up

Closed 2022-03-04.

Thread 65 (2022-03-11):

Deck Support Clip STL Labeled wrong

AleXthePunK, 2022-03-11:
For the Trident STLs, the deck_support_3mm_x8 and deck_support_4mm_x8 are backwards.

blite, 2022-03-18:
Are these shown inserted backwards in the manual as well? The manual seemed to match the CAD when I checked this, but I could not get them installed the way shown with deck_support_3mm_x8 and a 3mm panel Mandala Rose Works panel.   If am going to try the model for deck_support_4mm_x8 installed backwards.

AleXthePunK, 2022-03-23:
The manual is right, the labels on the STLs are backwards.

stvptrsn, 2022-04-10:
@blite The actual parts were a last second change so didn't get reflected in the manual.  They work the same though, just having one leg longer makes it easier to twist them in to place and made some room for the zip tie anchor point.

Is the reported issue that the file names are switched? The 3mm labeled part should be taller for the 3mm thick deck panel.  The 4mm part has extra room for a thicker panel.  I've double checked the parts and they are named as I would expect them to be.

stvptrsn, 2022-05-02:
Cleared this up in Discord chat.  The parts are labeled correctly.  All panel related stuff are named for the total panel thickness they go with (panel plus foam when applicable)

Closed 2022-05-02.

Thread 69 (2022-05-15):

SSR wiring diagram, page 211/215 of the Trident manual

1980alexGS, 2022-05-15:
Just wanted to mention that the diagram on page 215 confused me. I may be wrong, but it appears the AC supply socket is wired to the ‘Load’ side of the SSR. Please refer also to page 211.

I think all the other wiring diagrams are perfectly clear, but this one I feel could be clearer. Thanks!

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

1980alexGS, 2022-05-22:
Thank you DunarDolorgiet and KiloQubit - the reworked manual (using the Wago connectors) is so much clearer now. I may have been wrong and it was clear enough before, but I am really impressed how quickly you have improved it and removed all ambiguity. Cheers, -Alex

Closed 2022-05-19.

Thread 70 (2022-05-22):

manual inverted G and F Extrusion

Frigolol, 2022-05-22:
seems like page 147 is pointing G as F and F as G extrusion

BerzerkaDurk, 2022-05-22:
Clips from the manual, for clarity.

According to the diagram on pg 13, the G extrusion is the long front bed support extrusion, and F is the short center bed extrusion.

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

pg 147 has them labeled backward

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

Closed 2022-08-16.

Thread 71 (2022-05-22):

nuts are missing, pg 132

BerzerkaDurk, 2022-05-22:
Specification and installation of the 2 M3 hex nuts on the carriage halves, corresponding to the M3x40 and M3x30 S.H.C.S.'s are missing.

I would assume that, for ease of installation, the nuts would be pushed into the holes in a previous step, but page 132 is where the corresponding screws are installed

I humbly suggest that placement of the 2 M3 hex nuts be added to page 122.

Closed 2022-08-16.

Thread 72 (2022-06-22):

Filtered Inlet latches on wrong side of panel

iplayfast, 2022-06-22:
When using the Power_inlet_adamtech.stl The latches to hold it in place are located on the inside frame instead of the outside. It will latch if you put it in backwards :)

Also assembly manual should be updated for using the adamtech.

iplayfast, 2022-06-23:
Nope, it's correct. (Dumb user error).

iplayfast, 2022-07-01:
Not valid Issue

Closed 2022-07-01.

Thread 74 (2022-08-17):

README discrepancy. Build of Material vs Bill of Material

dougshell, 2022-08-17:
The readme states that you can find the "build of materials", but I believe this should read as "bill of materials". "Web site" is most often spelled as one word as well, but this isn't as big of an issue. The two-word variant is possibly influenced by the word "web page"

I know everyone wants to contribute to the VORON project and be well compensated. I'll take my payment in either Voron parts or thoughts and prayers!!!

"# Voron Trident

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

The official release of the Voron Trident 3D printer.  You can find the Build of Materials in the configurator located at the [Voron Design]( http://vorondesign.com/voron_trident) web site.  The recommended sizes for this printer are 250x250x250, 300x300x250 and 350x350x250."

nemgrea, 2022-10-11:
https://github.com/VoronDesign/Voron-Trident/pull/85

Closed 2022-10-11.

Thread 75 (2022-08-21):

Two hole chain wire anchor is mistakenly named 3 hole

rlaferla, 2022-08-21:
https://github.com/VoronDesign/Voron-Trident/blob/VTr1/STLs/Gantry/chain_wire_anchor_a_3hole.stl

chain_wire_anchor_a_3hole.stl => chain_wire_anchor_a_2hole.stl

rh101, 2022-09-03:
Are you sure this is a mistake? From my understanding, this STL is used with the generic 3-hole cable chain, which is why it has "3hole" in the name, since those cable chains don't come with an anchor point/strain relief.  The name of the STL doesn't actually have anything to do with the number of screw holes in the model.

Closed 2022-10-11.

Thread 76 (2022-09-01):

[Manual] Missing items and corrections

rh101, 2022-09-01:
Page 216: "Power Inlet" title is not aligned correctly, so it is off the page.

Page 217: Roll-in M3 nuts are missing from the diagram for the power inlet printed part mounting to the frame.

Page 232: Controller board jumper settings steps 3 and 4 do not match the highlighted section of the board.  They should be switched around.  In the diagram, 3 is the probe voltage setting, and 4 is the fan section.

iitsalex, 2022-09-19:
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
Page 13 also has a typo on "Length"

Closed 2024-02-09.

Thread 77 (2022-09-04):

[Manual] Use of 110 Y Alignment spacer

Slusnik, 2022-09-04:
Page 17  "Alternatively you can print the spacer that is included in the released files"
- No mention of how to use this spacer
- I take it you have to install the upper frame parts and then use the spacer between top an Y?

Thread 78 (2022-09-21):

[Manual] page reference on Page 182 is incorrect

wrwindsor, 2022-09-21:
"... skip the wire cover and follow the instructions on page 174."

Should be:

"... skip the wire cover and follow the instructions on page 190."

Closed 2024-02-09.

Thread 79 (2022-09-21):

[Manual] mini12864 case hinge needs accent "Voron heart"

wrwindsor, 2022-09-21:
mini12864 hinge piece is an accent piece per the [a] in the STL filename.

It should get a Voron heart in the manual (Page 274).

Closed 2024-02-08.

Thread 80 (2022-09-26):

Manual and BOM disagree on M3 FHCS with Power Inlet mounting

wrwindsor, 2022-09-26:
Manual on page 216 (Power Inlet) says to use two M3x10 FHCS.

M3x10 FHCS doesn't exist in the BOM.

M3x12 will work here, even if a touch too long for appearances, and M3x12 FHCS is in the BOM.

Dunno if BOM or Manual issue.

nemgrea, 2022-10-11:
bom change submitted

Closed 2022-10-11.

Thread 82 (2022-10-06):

Mains inlet wiring on p236 is backwards

wrwindsor, 2022-10-06:
If you're looking into the plug end of the mains inlet wiring, ground tang up, "neutral" is on the left and "line" is on the right.

see: https://www.electronics2000.co.uk/pin-out/iec.php (IEC 63020 pin assignment for C13/C14)

Therefore, if you're looking at the back of the filtered inlet (for purposes of running wiring), ground tang up, it is reversed -- the "line" tab is on the right and the "neutral" tab is on the left.

The wire coloring in the drawing on p236 is backwards of this.

rh101, 2022-10-07:
I was about to post about this issue as well.

FYI, the Voron 2 manual shows it with the correct wiring.

rh101, 2022-10-07:
It's definitely incorrect in the Trident manual.  The Voron 2 manual shows it with the correct wiring.

BerzerkaDurk, 2022-11-10:
This has happened before. Issue #45. It was fixed then, but it looks like at some point between then and now, they flipped the orientation of the power inlet 180 degrees in the manual, but they didn't swap the wire colors.

Previous manual, correct wiring:
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

Current manual, incorrect wiring:
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

BerzerkaDurk, 2022-11-10:
I'm going to start an engineering ticket on the Discord. This needs to be corrected immediately. It's a fire hazard. If someone is using the single fused inlet, wired backward, and there is a short to ground, it will short the hot wire right to ground with no fuse protection.

BerzerkaDurk, 2022-11-10:
It should be noted that the wiring on page 237 will have to be corrected, as well.

SirOink, 2023-05-11:
still hasn't been fixed, may 11th 2023. I see this as a major issue due to the amount of low quality kits out and about combined with self-sourcing from non-eu/us countries (the bom filtered power inlet is hard to find in some places, let alone dual fused filtered inlets)

luckily I'm pedantic about safety, I read my power inlet's data sheet & googled IEC ordering, else I'd have fell for it too as I'm
a. dyslexic
&
b. don't like watching 4 hour long (or even 10 minute long) video tutorials. I prefer written ones, so the manual has been my gospel. I'm surely not alone, hopefully the others have backup fuses bc the devs don't seem to care about updating the trident manual/trident seems to be the red headed stepchild 🤷‍♂️

nemgrea, 2024-02-08:
fixed

Closed 2024-02-08.

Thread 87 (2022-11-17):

Thumb...bolts?

shiftingtech, 2022-11-17:
Manual page 158 refers to the spacers as Thumb Bolts.  I don't think this is accurate, I think they should be referred to as "thumb nuts" or "knurled nuts".  This both better matches the BOM, and more accurately represents the object at hand.

Closed 2024-02-08.

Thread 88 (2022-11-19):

BOM is missing "Foam Tape" entries, both 1mm and 3mm

wrwindsor, 2022-11-19:
Manual shows and specifies Foam Tape 1mm (back and top panels) and 3mm (side panels)

Not in the BOM.

I admit that this is a minor nit, but I can't set that tag.

cmdremily, 2023-05-14:
I wouldn't call this a minor nit, it's quite an annoyance as my build is delayed again... xD

Also the manual doesn't spec the width of the foam tape, and it isn't clear that th 1mm/3mm refers to thickness.

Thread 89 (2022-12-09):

Voron trident losing communication with mcu and ends the print after 50+ minutes

piertek, 2022-12-09:
Hi, I'm having issues with printer quirting printing at random time, sometimes after 50 min some  after 2 hours, today just now it stopped twice on different prints, the screen loses the image on the tft and the connection with mainsail shows this: Klipper reports:
SHUTDOWN
Lost communication with MCU 'mcu'
Once the underlying issue is corrected, use the
"FIRMWARE_RESTART" command to reset the firmware, reload the
config, and restart the host software.
Printer is shutdown.
i have being told last week that it was a usb connection problem so i search for it and changed the usb, yesterday night we updated Moonraker dependencies and today the first fail was after 2 something hours.
is a voron trident 300, running huvud canbus
i have being tracing temperatures from all mcu's and the highestone is the huvud topping at 70 degrees celsius printing abs in enclosure.
All i can understand from the logs is that klipper has shutdown.
Any help will be appreciated im desperate.
[klippy (26).log](https://github.com/VoronDesign/Voron-Trident/files/10198736/klippy.26.log)
[moonraker (20).log](https://github.com/VoronDesign/Voron-Trident/files/10198737/moonraker.20.log)

raymondh2, 2022-12-09:
Hello! Thanks for reaching out to us on GitHub. We use GitHub for managing design issues not troubleshooting. Try one of our other community sites below for troubleshooting help.

Discord: https://discord.gg/voron
Official Forum: https://forum.vorondesign.com/
Reddit: https://www.reddit.com/r/vorondesign/

Closed 2022-12-09.

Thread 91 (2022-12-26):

Screw used the wire cover on the A Drive is too short.

marcellomaia, 2022-12-26:
The recommended screw to attache the wire cover on the A Drive is too small.  Maybe a M3x10 instead of a M3x8 SHCS would be the right choice (page 261 of the manual).

nemgrea, 2022-12-27:
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
8mm screws seem to be of adequate length...

if your foam tape is thicker than 1mm that may be your issue?

marcellomaia, 2022-12-27:
I believe you did not understand the part I'm referring to.  I'm talking about the screw marked below,  the one the secures the wire cover on the A drive. The distance between the base of the screw to the top of the A drive is 7mm,  so an 8mm screw I believe is not appropriate.

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

nemgrea, 2022-12-27:
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
page 225 it looks like then

atoomnetmarc, 2023-10-13:
Current revision has the error on page 231. M3x8 did not fit, M3x12 did fit.

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

Closed 2025-06-15.

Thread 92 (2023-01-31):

a_drive_frame_lower and b_drive_frame_lower STLs are unusually large (>7 MB) comparing to other STLs

pajtaz, 2023-01-31:
As stated in the title, a_drive_frame_lower.stl and b_drive_frame_lower.stl are large comparing to _upper STLs in the same folder. Importing those two STLs in command line Plater, for example, always throws an error. They seem to be "fine" when opening in a slicer.

I recommend to check those files and see if something went wrong during export to STL. Current workaround for me was to export those files as STLs from the CAD.

HyJeremy, 2023-02-23:
Files were uploaded in STL ASCII format, rather than binary. I'm unsure how to convert, so it would be great if this were fixed

nemgrea, 2023-03-01:
fixed
https://github.com/VoronDesign/Voron-Trident/pull/101

Closed 2023-03-01.

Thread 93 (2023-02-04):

Terminology Mismatch between BOM, Assembly Manual and sourcing guide

chaos777b, 2023-02-04:
The Voron Assembly manual calls for a M5 Shim when putting together the A idler, page 26.
The generated BOM for the trident does not have an M5 Shim, but it does have an M5 1mm Spacer.
The souring guide list it as M5 1.0mm Thick Shim/Washer.

Side note the LDO kit has both precision M5 1mm spacer, and a M5 1mm washer.

Yay for terminology!

nemgrea, 2023-03-01:
BOM and SG have been fixed, next manual update will consolidate all three, for now "shim" is mentioned in all three locations

Closed 2023-03-01.

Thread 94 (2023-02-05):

Keystone module openings in the Skirt have the wrong opening size.

rselec, 2023-02-05:
Hi, I just figured out that the keystone module openings in the Skirt (of the official Trident VTr1 release) have the wrong opening size. My keystone modules fall out.

Opening for clip should be 14.9 x 19.5 mm and is 14.9 x 20.65 mm in the released CAD.

The opening for the front shall be 14.9 x 17 mm and is 14.9 x 18.85 mm.

I'll fix this for me and print the skirt part again. Will someone fix this in the next release? I use Design Spark Mechanical and cannot export a STEP file, STL will be added here.

rselec, 2023-02-05:
[keystone_panel_fixed_openings.zip](https://github.com/VoronDesign/Voron-Trident/files/10611529/keystone_panel_fixed_openings.zip)

rselec, 2023-02-05:
The Keystone Blank Insert is also wrong in size, it would be too large for the fixed openings, needs to be decreased by about 1.2 mm in height.

newphreak, 2023-04-22:
Tested, your fix fits like a glove.

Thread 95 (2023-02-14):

Extrusion lengths, including for a 250mm frame, are missing in Assembly_Manual_Trident.pdf

tkalbitz, 2023-02-14:
In the current manual of the Trident is the length for the different extrusions missing.  More precisely: The pages are missing. They were in the manual in the past see this "Steve Builds" stream: https://youtu.be/JWLwHDgkYPw?t=77

The lengths are needed to reference extrusions length and letters e.g on Page 13.  Additional on Page 13 in the manual is also a reference to the page "The length of marked extrusions depends on the build size. The size shown is for a 250 size Trident. Add 50/100mm for a 300/350 sized Trident."

tkalbitz, 2023-02-14:
One possible solution could be to reference on page 13 to the configurator on the web page and add in the configurator after every extrusion a note "Extrusion 'A' in the manual xx mm".

nemgrea, 2023-03-01:
they were replaced/removed intentionally by the current length diagram on page 13 due to the majority of the extrusion lengths being build size dependent.

the exact number measurements are not needed in order to organize the extrusion as it is shown on page 13

Closed 2023-03-01.

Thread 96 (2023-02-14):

Bed mounting: No information on how tight the bed mounting screws should be (described in 2.4 manual page 59).

tkalbitz, 2023-02-14:
After I discussed my bedmesh in discord someone mentioned that only one screw should be tight and the rest rather loose. This should be written in the manual. I followed the tip and my bedmesh improved.

After reviewing the Trident and the 2.4 manual: This step is missing in the Trident manual and written in the [2.4r2 manual](https://github.com/VoronDesign/Voron-2/raw/Voron2.4/Manual/Assembly_Manual_2.4r2.pdf) on page 59. It is also mentioned in the "[I wish I had known page](https://docs.vorondesign.com/community/howto/simonthecat/I_wish_I_had_known.html)" under Lessons -> Expensive

Closed 2024-02-08.

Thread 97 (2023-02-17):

Wrong screw in manual page 216

FlyingT, 2023-02-17:
On page 261 it says to use a M3x8 to attach the cable cover, but that screw is too short, barely clearing the printed part.
A M3x12 is needed.

https://ibb.co/dLKJ0d8
https://ibb.co/WBgnL6q

FlyingT, 2023-02-17:
duplicate to #91

Closed 2023-02-17.

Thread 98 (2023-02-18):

Initial Startup Checks: Mixed up X and Y

FlyingT, 2023-02-18:
[Define 0,0 Point (V0, V1, Trident, V2, Legacy)
](https://docs.vorondesign.com/build/startup/#bed-locating-v1-trident-legacy
)

X and Y is flipped, currently it says:
"The Z endstop should be located at close to max X position. Home X and Y with G28 X Y and then traverse just Y to locate a Z endstop position at the maximum X travel that will still trigger the endstop. Lock down the Z endstop at that position."

should be:
"The Z endstop should be located at close to max Y position. Home X and Y with G28 X Y and then traverse just X to locate a Z endstop position at the maximum Y travel that will still trigger the endstop. Lock down the Z endstop at that position."

FlyingT, 2023-02-18:
Duplicate to:
https://github.com/VoronDesign/Voron-Documentation/issues/300

Closed 2023-02-18.

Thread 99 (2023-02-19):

Manual: Explaination PTFE tube from holder to hotend is missing and when to use which tube.

tkalbitz, 2023-02-19:
It is unclear when to use bowden and when to use PTFE tube. Both are in the manual, but bowden tube is never mentioned (quick search in the manual showed no result)

Additional questions I had: When to use which PTFE tube. Is a two part setup: One PTFE part to the coupler a second from the coupler to the hotend? Answer no you just push the PTFE tube from outside into the coupling to the hotend and into the extruder. This step is missing as "last page" of the manual.

After a few days someone pointed out that on page 313 the PTFE tube should go in the circular cutout in the holder. I was thinking the square cut out is for a prealignment for the PTFE tube.

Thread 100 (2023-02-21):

Trident Configurator has wrong Cable Chain amount

ccfman2004, 2023-02-21:
When I get the BOM for a 350mm Trident the configurator lists a 1 meter 10x11mm cable chain with 2 end sets but the manual has you install 3 chains. Am I just misreading the BOM?

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

Closed 2023-03-01.

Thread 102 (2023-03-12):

Invalid Record Index in assembly step file

Leafy1, 2023-03-12:
When opening the assembly step file in solidworks 2017 it fails while trying to import the second item in the step file with the error that the record index is invalid. Could someone re-generate that step file and re-upload it?

nemgrea, 2023-03-13:
this is a solidworks issue. in your import settings uncheck the 3D Interconnect option and it should import just fine

Closed 2023-03-14.

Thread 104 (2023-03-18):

BOM should also include a terminal cover for the 5V PSU

dekay, 2023-03-18:
The BOM has a "Mean Well TBC-09 Terminal Cover" for the "Mean Well LRS-200-24 PSU" but it **does not** include one for the "Mean Well RS-25-5 PSU".  It really should include one given that this is a safety issue and it costs pennies.  The Mean Well cover is also better than a printed version because it is transparent, allowing you to see the screw terminals.

The appropriate cover for the 5V PSU is TBC-05 and [it is available at Digikey](https://www.digikey.ca/en/products/detail/mean-well-usa-inc/TBC-05/7707107).

tkalbitz, 2023-04-20:
Or a printed version could be used: https://mods.vorondesign.com/detail/jyO8bHoPTy3XUaYlXscB7w

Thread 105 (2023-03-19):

Manual: Hall Effect Endstop link

MallocArray, 2023-03-19:
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

Page 48 under "Hall Effect Endstop" has a link text, but the link if you click on it is incomplete. It attempts to only go to https://voron.link without the rest of the URL.  Hovering over the final line is not treated like a link at all.

This is using the built-in PDF viewer in Edge

MallocArray, 2023-08-19:
Fixed in latest manual release

Closed 2023-08-19.

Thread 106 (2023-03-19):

Manual: The Voron Belt Path link

MallocArray, 2023-03-19:
Page 119
In the middle of the page is a URL address about CoreXY that is formatted as a link, and hovering over the text in the Edge browser PDF viewer changes the cursor, but no link address is specified and clicking on it does not result in opening the address.

Manually typing the address does take you to a valid site, but it is not properly formatted as a link in the PDF

Same behavior in Edge and Adobe Acrobat Reader

MallocArray, 2023-08-19:
In the most recent manual version this issue is still present in Edge in Windows 11

ChopperRob, 2023-10-15:
Same issue with the "Hall Effect Endstop" link on page 137

Closed 2024-02-08.

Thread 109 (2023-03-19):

Manual: Jumper install mislabled

MallocArray, 2023-03-19:
Page 232

Text says 3) is for setting the Fan Voltage, but in the image, the fan jumper location is labeled 4

Text says 4) is for setting probe voltage, but in the image, the fan jumper location is labeled 3

These two should be flipped around.

Compared to the previous page where the jumpers were removed, an improvement would be to keep the same step numbers where possible.  This would mean possibly changing Page 231 to the order of
1) Drivers
2) Fan Voltage
3) USB Voltage
4) Probe Voltage
5) LED Voltage

Then in page 232, only the final step would need to deviate if reordered
1) Driver jumper location
2) Fan jumper location
3) USB jumper location
4) Probe jumper location
5) Wirejumper for 24VDC on far right

Finally, on Step 5, it says "wirejumper" and this could be improved to be 2 separate words "wire jumper"

Closed 2023-08-19.

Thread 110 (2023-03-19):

Manual: Toolhead PCB link does not work

MallocArray, 2023-03-19:
Page 253

QR code and URL below it are not valid links.  Cursor does change when hovering over it, but no address is shown in the lower left corner and clicking on it does not take you to the address.

Both Edge browser and Adobe Acrobat Reader

QR code is valid and works as expected.

MallocArray, 2023-08-19:
QR code removed in latest manual version

Closed 2023-08-19.

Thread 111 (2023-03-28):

Manual: Page 15 Extrusion misspelled

MallocArray, 2023-03-28:
Page 15

The label for "C Extrsuion" is spelling incorrectly and should be "C Extrusion"

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

MallocArray, 2023-08-19:
Fixed in [79750725c457ceb16260322cf83922eb3b04ed33](https://github.com/VoronDesign/Voron-Trident/commit/79750725c457ceb16260322cf83922eb3b04ed33)

Closed 2023-08-19.

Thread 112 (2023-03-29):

power_inlet_filtered.stl cad issue?

leesafur, 2023-03-29:
Not enough thickness for the bottom hole?
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

newphreak, 2023-04-22:
This is correct, 0.4mm difference from the middle and keystone skirt pieces on those bottom 3 partial hexagons.
https://cdn.discordapp.com/attachments/698953981023486012/1099131556087463996/skirt.gif

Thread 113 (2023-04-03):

Manual: Typo on page 15

Tuxedo-VE, 2023-04-03:
The blue label next to the C extrusion says "C Extrsuion"
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

nemgrea, 2023-04-05:
repeat issue form https://github.com/VoronDesign/Voron-Trident/issues/111

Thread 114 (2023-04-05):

Manual: Hall Effect Endstop not applicable?

MallocArray, 2023-04-05:
Page 48 in the manual has an option for removing a part if using a hall effect endstop, along with a link to documentation.  Visiting the link  https://voron.link/hxd3cv0 goes to a page where the first sentence says
"The hall effect endstop is only designed for a V2.4. It will not work on any other models!"

If this is not applicable to the Trident, then suggest the mention in the manual be removed entirely.
If it could be applicable to the Trident, then this linked page should be updated to mention the Trident as well.

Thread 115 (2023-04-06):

With the popularity of CANbus mods, it could be helpful to document alternate endstop mounting.

BerzerkaDurk, 2023-04-06:
I know that CANbus is a mod, but since the provisions for alternate endstop microswitch location are included with the official release, I feel like it's relevant to possibly include them in the build manual. Perhaps in an appendix.

Specifically, /STLs/Gantry/AB_Drive_Units/[a]_y_endstop_housing and the alternate location of the x-axis endstop on the back of the carriage.

HitLuca, 2024-03-08:
Wanted to remove my y axis cable chain and ended up with exactly this issue, there's no mention anywhere of this alternate endstop mounting

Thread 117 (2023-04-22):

Trident r1 "power_inlet_filtered" bug/fault

Exerqtor, 2023-04-22:
Don't know if it's been mentioned before, but since it haven't been comitted an fix to it i'll mentioned once again in that case:

It's a bug/fault in "power_inlet_filtered", both in CAD and .stl where the lower honeycombs are 0.4mm to deep, resulting in the heatset hole breaking through the top surface of the body.

_I've fixed in "my" CAD, but since it's litterlarly a 2 second fix it I bet who ever on the DEV team ends up doing this will find it easier to do it in CAD themself rather than importing a .step i post here._

### Images for reference:
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

newphreak, 2023-04-22:
Duplicate of #112

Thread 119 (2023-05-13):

Wiring PE to frame does nothing.

cmdremily, 2023-05-13:
On page 238 of the Trident assembly manual, the instructions show the PE being connected to the frame without further instruction.

While it is correct from an electrical safety standards point of view to connect any electrically conductive casing of a device to PE. In practice, the aluminium extrusions used on the absolute majority of builds are anodized and that makes the surface of the extrusion non-conductive (just like paint is). Don't trust me? Pick up a multi meter and measure two points on the surface of your nearest anodized extrusion. You'll find the surface has really poor electrical conductivity.

What this means is that simply screwing the PE wire to a roll-in t-nut on the frame (which is what I perceive as the intended solution) might not actually connect the frame to PE unless the bolt used scratches of the anodization and makes electrical contact this way. But there is no instruction to this end.

Furthermore, because of the blind joints design, it's likely but not guaranteed that extrusions that are joined make electrical contact via either the screw and the exposed aluminium in the non-threaded through hole or by scratching the anodization of the non-threaded extrusion. Again, subject to if the screws are anodized themselves. In my build, they do make electrical contact with the exception of the back side horizontal member between the A/B motor mounts.

I would like to see this section of the manual improved to mention both the recommended fastening technique (as it's not obvious to many people that the extrusion isn't conductive) and to use a multimeter to check conductivity from various frame elements to the PE connection (e.g. PSU casing).

melufre, 2023-05-13:
hello
from my recent expérience don't succeed to get a good contact using T-nuts but  using hammerhead and tigth them strong i was below 3 ohm betewn 3 contact points

rbricheno, 2024-05-13:
Slightly abrading the surfaces of the extrusion works great. This should really be done at all points where two extrusions join. I did this and my whole frame is now continuous and easy to earth. At the very least this should be recommended for the wire from the Wago to the frame.

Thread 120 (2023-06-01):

Thumb bolt/ Knurled nut wrong size in manual?

Faenum, 2023-06-01:
The knurled nut/thumb screw for the bed on the manual says M4 (and thats what has come in the kit) But every other part (screws/tnuts etc) are all M3 and none of it wants to fit together.
Is the manual wrong in that it should be an M3 knurled nut/thumbscrew?

timmit99, 2023-06-01:
Nope, the manual is correct. That m4 nut is used as a spacer. You don't actually thread into it but it just acts as a spacer to stand the bed off of the extrusions.

Faenum, 2023-06-01:
Thanks
In that case the bolts are too short. It says m316 but theyre not long enough to reach the Tnut

Faenum, 2023-06-01:
We worked it out, the LDO kit does come with a thicker bed that needs M3x20

ccfman2004, 2023-06-02:
The Build Plate PDFs mention a bed thickness of 6.5mm to 9.5mm thick which means the M3x16 bed screws are too short if your bed is thicker than 6.5mm. The manual should mention you need M3x20 if your bed is 9.5mm thick as many beds from the recommend US online resellers are 9.5mm thick.

Faenum, 2023-06-04:
Yeah, I couldnt find anything in the manual about that, just says use m3x16 screws. It could be written elsewhere though.

Closed 2024-02-08.

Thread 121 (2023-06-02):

Manual: Page 217 does not mention roll-in T-nuts

MallocArray, 2023-06-02:
Page 217 shows installing the Power Inlet skirt, and shows the screw size, but at this point in the manual, it has not mentioned adding any roll-in t-nuts to the frame for the skirt components.  It is shown as present in the images, but in all other places the nuts are called out when to install and which way to face them, but this is not shown in this case.

Add the orientation of the nuts and that they need to be inserted at this point.

MallocArray, 2023-08-19:
Addressed in latest manual

Closed 2023-08-19.

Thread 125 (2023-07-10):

Sensorless config

cmdtbalbosa, 2023-07-10:
Greetings friends, I hope you are well.

I'm trying to install klipper but I'm having trouble configuring sensorless. Does anyone have any tips or references to help me?

I'm using a SKR 1.4 turbo with EXP mot
and using voron trident's printer.cfg.

Closed 2023-07-10.

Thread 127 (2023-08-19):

Manual: Jumper remove/install ordering suggestion

MallocArray, 2023-08-19:
There is an inconsistency between the labels and order of removing jumpers from the board and installing the needed ones.

Page 203 covers removing jumpers in this order
1. Driver
2. Fan Voltage
3. USB 5V
4. LED Voltage
5. Probe Voltage
6.
The next page mentions 4 of same jumpers, but in a different order
1. Driver
2. USB 5V
3. Fan Voltage
4. Probe Voltage
5. Unlabeled 24v jumper

Compared to the previous page where the jumpers were removed, an improvement would be to keep the same step numbers where possible. This would mean possibly changing Page 203 the order of

Drivers
Fan Voltage
USB Voltage
Probe Voltage
LED Voltage
Then in page 204, only the final step would need to deviate if reordered

Driver jumper location
Fan jumper location
USB jumper location
Probe jumper location
Wire jumper for 24VDC on far right

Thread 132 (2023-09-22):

Trident Manuel still has Afterburner parts and instructions in the X Axis section

Deadbob1978, 2023-09-22:
page 98 of the manual (X axis) still has artwork and directions for the Afterburner carriage instead of the parts (and extra heat sets) for Stealthburner and Clockwork 2

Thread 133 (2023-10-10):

Manual: 300mm bed frame spacing.

atoomnetmarc, 2023-10-10:
Hi,

I am assembling a Trident 300, is it possible that the suggested 175mm spacing for the F-extrusion should be 25mm more when assembling a Trident 300?

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

Just like this:

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

nemgrea, 2024-02-09:
Duplicate of #77

Closed 2024-02-09.

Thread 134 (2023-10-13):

Manual: controller board wrong link

atoomnetmarc, 2023-10-13:
Link says docs.vorondesign.com, link goes to this repository.

Suggested link: https://docs.vorondesign.com/build/electrical/#trident

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

nemgrea, 2024-02-09:
pg 203

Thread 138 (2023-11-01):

Typo on Trident Manual Page 4

shaunmorris, 2023-11-01:
"provided the following prwint guidelines for you"

prwint should be spelled print

Incidentally, where is the source for this?   I wasn't able to find it, or I would have provided a fix, rather than just a bug report.

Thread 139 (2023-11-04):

Manual: Page 100

webRat, 2023-11-04:
Middle diagram is missing 2 heat set inserts at the top.
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

I realize that these instructions are in the stealthburner manual. I would argue that... I read/completed page 100 before I even had to reach page 162-163 to go read the stealthburner manual.

webRat, 2023-11-04:
This might be a duplicate of https://github.com/VoronDesign/Voron-Trident/issues/132

Closed 2023-11-07.

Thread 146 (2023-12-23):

Wrong extrusion suggested as spacer on page 17

rafal-molotkiewicz, 2023-12-23:
Page 17 calls to use Extrusion E as a spacer. Extrusion E is horizontal and spec-dependent. It is OK on 250 spec, as the E has 330mm, but on 300 and 350mm spec E is 380 or 430mm long, respectively. Information that it only works for 250 spec should be more prominent, at least.

With a little rearrangement of the assembly order, I was able to use Extrusion H as a spacer, something that's faster, cheaper and more friendly to the environment than printing something that will be used only once and then discarded, Please consider it as an option.

nemgrea, 2024-02-09:
Duplicate of #77

Closed 2024-02-09.

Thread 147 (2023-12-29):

No puedo hacer funcionar mi impresora me marca error moonraker y no se programar

Rominadesign, 2023-12-29:
Ya seguí los pasos que. Te dice como instalar el firmware de klipper en mainsailos pero me aparece error de conexión klippi y no sé cómo solucionar lo mi impresora es una voron Trident de 350

nemgrea, 2024-01-09:
please us the help channels on the discord or the forums for troubleshooting

Closed 2024-01-09.

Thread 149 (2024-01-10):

[Manual] Clarification bolting x-axis to y-rail, and inconsistency in "end stop" terminology

dekay, 2024-01-10:
The section on the X Axis Assembly says "Missing some bolts?  The other two bolts will be installed later".  Not only is this vague, but it is _much later_, like 86 pages later when the XY End-Stop Pod is installed.  It would be better to reference this more directly: "... The other two bolts will be installed with the mounting of the XY End-Stop Pod."  That way the user can at least search the doc for "XY End-Stop Pod" and find the reference.  By the way, some kits like the MPX one don't have this pod in the first place.  It then becomes more obvious to the user that all four bolts for the X Axis Assembly could be installed at the same time for their kit.

Also, the manual is inconsistent in its terminology.  Sometimes it uses "endstop", other times it uses "end stop", and yet other times it uses "end-stop".  This makes searching the PDF for this term very hit and miss.  Pick one spelling ("endstop" is simplest) and use it throughout.

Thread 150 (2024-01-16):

RPi 5 active cooler does not fit with raspberrypi_bracket.stl

slashbeast, 2024-01-16:
Hi,

The active cooler for Raspberry Pi 5 comes with plastic push-pins that sticks quite a bit on the back, and the location for them are exactly next to the mounting holes. Since this cooler is came out together with RPi5 it is safe to assume many people will go with it, and therefore run into the issue. It appears to me that adding just 1 mm to the raised standoffs would solve the problem, as it is almost flush, perhaps 2 mm to be safe.

This is not Trident specific, since all other repositories like V0 or v2.4 will have the same issue. It can also be challenged that using RPi5 for Klipper is massive overkill and hardly anyone will do it therefore this is not considered a problem, however with RPi5 finally providing simultaneous 5Gbps on each USB-A 3.0 ports I can see people that used high bandwidth cameras and canbus to move to it, those that suffered from communication looses due to USB bus working at it's capacity on RPi4.

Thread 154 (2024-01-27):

Issue with extruder. It freezes up when printer is powered and won't work when activated

HeATThER, 2024-01-27:
I've tried everything. swapping cables, motors, drivers, and ports to troubleshoot the problem, but nothing is working, leaving me thinking that it must be in the config. This is a new build. The extruder worked last week on a small test run, but after I troubleshooted and calibrated some other things, it now freezes when I power on the printer. I'm truly at a loss on this and need some guidance. The only thing I remember doing out of the ordinary is updating Klipper, Moonraker, and such. It comes with a warning that it can make changes to the system, but I wouldn't know exactly what all the updates did. That stuff is a little above my head.

Thanks for taking a look at my code. I really do appreciate the help. My social network for 3D printing is me and google. XD And I've about exhausted my resources on this one.

[printerconfig.txt](https://github.com/VoronDesign/Voron-Trident/files/14073458/printerconfig.txt)

HeATThER, 2024-01-29:
After some fiddling, I found the problem. I needed ! on the en pin.

timmit99, 2024-01-29:
That would do it! Since the example config has it I'm assuming it just got accidentally deleted during your attempts to get the motor working :-)

Glad to hear it's resolved!

Closed 2024-01-29.

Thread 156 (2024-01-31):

Website: build/startup: Motor-Check make it clear.

calmarc, 2024-01-31:
What is: move one millimeter in a positive direction?

What is positive? Maybe when you know how the coordinate system is about, but how would you know?
Why not say: Move on millimeter in a positive direction, meaning to the right towards the endstop.
or similar.

Actually there is something written like: If the endstop is at 0.... .. yeah once you understand everything, everything makes sense. With lots of if's then then. Just not obvious when you are noob.

Likewise, what does that mean: stepper_x 	The motor will rotate clockwise first, then back counterclockwise

What is a clockwise rotation of a motor? Is it from the point of the view of the motor itself, or from some other point of view? Obviously it's meant when you look down towards the motor - I guess?

And once you have it wrong, like I had, you are going through all this though-processes and it ends up being ambigious. Exactly what it is not supposed to be.

My English is too bad to get it properly how it would be clear, but yeah well.

thanks a lot either way.

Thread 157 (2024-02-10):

Manual should instruct that T-nuts be preloaded prior to frame assembly

kozross, 2024-02-10:
The fact [this video even exists at all](https://www.youtube.com/watch?app=desktop&v=hpkN9NHoKiY) suggests that many people find it difficult to load T-nuts into extrusions with the frame already assembled. It wouldn't be difficult to make this preloading the first step, before assembling the frame, and would save people (including me!) a lot of frustration. I'm basically gonna have to take apart my frame, which I spent no small amount of time squaring, because I will need to preload T-nuts, and I'd rather save future builders the hassle.

Alternatively, the manual should clearly specify how you are supposed to load T-nuts into an already-assembled and squared frame, as it currently fails to do that.

JustAManDoingGit, 2024-03-07:
The point of that nut is to be a drop-in installation of nut (not needing to preload it). The problem seems more like a mismatch of nut used for your specific extrusion. I never really had problem installing those.

Closed 2024-12-18.

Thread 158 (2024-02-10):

The A and B idlers are needlessly annoying to assemble

kozross, 2024-02-10:
The combination of having to hold the bearing stacks still while getting a part situated, threading another screw in, _and_ not losing a captive nut, feels excessive and unnecessary as a design choice. I understand that there are limitations to what is possible, but surely something better than this could be done?

JKtech3D, 2024-03-10:
Maybe take a look at [Clee's Beefy Front Idlers](https://github.com/clee/VoronBFI)

kozross, 2024-03-10:
@JKtech3D - I already did, and chose to use them instead. Why they're not stock, I have no idea.

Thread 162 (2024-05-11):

Missing STL part in skirt

oldcarlos, 2024-05-11:
I can't seem to find the STLs for Skirt>Middle_Fan_Support, both here and in the VT.zip file. I will save a mesh from the CAD file, but it seems odd it is missing.

nemgrea, 2024-05-12:
is this the part youre looking for?
https://github.com/VoronDesign/Voron-Trident/blob/main/STLs/Skirt/side_fan_support_x2.stl

oldcarlos, 2024-05-12:
This is embarrassing. I can hear my wife complaining how terrible I am at looking for things. Yes, it is, and it was right there only with a different name than on the CAD.

nemgrea, 2024-05-12:
im going to keep the issue open since those names should match

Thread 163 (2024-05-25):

Line 172 of Kraken config has a typo: sstep_pin: PG11 instead of step_pin: PG11

GreenPlasticWaterCan, 2024-05-25:
Line 172 of Kraken config has a typo: sstep_pin: PG11 instead of step_pin: PG11.
This caused klipper to error out.

nemgrea, 2024-05-25:
https://github.com/VoronDesign/Voron-Trident/pull/164

Closed 2024-05-25.

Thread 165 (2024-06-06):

Manual: X carriage lacks two heat inserts

Icenowy, 2024-06-06:
The current Trident manual (at commit 4d8b81a5f9a9503415e8aea0b84269de35c69dbe), at page 100, has a page of preparing the two parts of X carriage attached on the MGN12H carriage.
However, the Stealthburner manual (at commit 8285659a77016b63c2f27befe9a23f2907c28b3b) at page 59, shows the preparing of the same parts, with two more heat inserts, which are required to mount the Clockwork2 extruder. These two heat inserts are missing on Trident manual, which leads to me inserting them after the carriage is installed and belts fastened when following the Trident manual.

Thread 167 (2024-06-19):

Manual page 8 : it shows the 625 bearings while the trident does not have any.

Nimajine, 2024-06-19:
Hello !

It's not very important but there is a small error, page 8 : it shows the 625 bearings while the trident does not have any.

It is important to point out that this manual is a beautiful and hard work! congratulations.

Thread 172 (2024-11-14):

Horizontal Line keep repeating (Voron Trident 250)

Daehyoun, 2024-11-14:
Interesting symptom....
In my rectangular lithophane printing, my new Voron Trident 250 printer has some strange issue.

Certain layer was shifted and this symptom happens at every  3~3.5mm
Printer is Voron Trident 250 and just assembled and started to print and test it.
I thought CoreXY bed will not shifted horizontally, and there will not be this issue.
But, happened....

Any idea to try to improve this issue?

Thanks

Daehyoun

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

nemgrea, 2024-11-18:
this would be perfect for a help ticket on the discord or a post on the forum to get help from the community. it looks like this is a user specific issue and not a printer design issue.

Closed 2024-11-18.

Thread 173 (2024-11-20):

bowen_retainer.stl -> bowden_retainer.stl spelling fix

thunderkeys, 2024-11-20:
STLs/Spool_Management/bowen_retainer.stl

should probably be

STLs/Spool_Management/bowden_retainer.stl ?

nemgrea, 2024-11-20:
https://github.com/VoronDesign/Voron-Trident/pull/174

Closed 2024-11-20.

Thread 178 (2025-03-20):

Bottom panel clip does not fit side fan support

twbaumann, 2025-03-20:
_Panels/bottom_panel_clip_x4.stl_ with a beveled edge of 35/55° extends into _Skirt/side_fan_support_x2.stl_ with 45° bevel.
Screwing the parts together results in an angled position of the side panel clips which puts force on the VHB tape connection to the bottom panel.

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

I fixed this for my Trident by creating a new file [_bottom_panel_side_clip_x2.stl_](https://github.com/twbaumann/Voron-Trident/blob/dde81106ab0f52e0b6a257bf3d6acaa210bddc6b/STLs/Panels/bottom_panel_side_clip_x2.stl) by differencing with _side_fan_support_x2.stl_ in OpenSCAD.

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

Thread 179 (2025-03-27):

Vivedini Marathon IDEX 3d printer

jpainter6865, 2025-03-27:
I recently purchased a new Marathon printer. In attempting the calibration routine as described in the assembly instructions, I managed to short out the mother board. ( I know, stupid and costly mistake). I ordered a new BIGTREETECH Manta M8P V2.0 board for a replacement. I have exchanged multiple emails with customer support, but the language barrier is hindering me from getting a novice like me the information I need. After watching numerous YouTube videos on how to flash the firmware, etc. I'm no closer to a solution and getting my printer operational. Where can I find the information I need and specific instructions on software installation? Looking at some of the postings on GitHub I can see where my request seems rather juvenile, but I sincerely need some help so my $1500 investment doesn't end up on the trash heap. HELP. Thanks!

bdbell, 2025-03-27:
I've never heard of that printer, but I'm sorry for your trouble. If you need support I strongly recommend heading over to the Voron Discord and asking for help there. The GitHub issues are focused on design problems with the specific printer.

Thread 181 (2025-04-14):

Rename files xy_joint_*_MGN12.stl --> xy_joint_*_MGN9.stl

jdspugh, 2025-04-14:
These files should be named with the postfix MGN9 rather than MGN12 since the STLs are sized for MGN9 blocks:

xy_joint_left_lower_MGN12.stl
xy_joint_left_upper_MGN12.stl
xy_joint_right_lower_MGN12.stl
xy_joint_right_upper_MGN12.stl

shiftingtech, 2025-04-14:
the MGN12 refers to the size of the X carriage, and is correct.  (since mgn9 is the only size rail that's only been supported on the Y axis, there's no need to distinguish that)

hartk1213, 2025-04-14:
> These files should be named with the postfix MGN9 rather than MGN12 since the STLs are sized for MGN9 blocks:
>
> xy_joint_left_lower_MGN12.stl xy_joint_left_upper_MGN12.stl xy_joint_right_lower_MGN12.stl xy_joint_right_upper_MGN12.stl

To add to what shifting said above, the belt path on the XY joints for mgn9h vs mgn12h for the X rail is different that's why there are 2 different sets of xy joints

jdspugh, 2025-04-15:
Thanks for looking into this.

I'll detail my case here as an end user (which perhaps I should have done earlier):

For the Y axis my supplier sent 2xMGN12 rails instead of 2xMGN9, so I downloaded the *Voron Trident XY Gantry Conversion to MGN12H Rails* (https://www.thingiverse.com/thing:5124692) mod. When sending to get the parts printed I accidentally sent the STLs for the original Voron Trident parts. Cause of the MGN12 naming I thought they were the mod parts. I thought the filename would relate to the individual part being printed cause for those individual parts (separated from their overall function/group) they are directly related to the MNG9 Y axis rails.

I guess something like MGN12x_MNG9y_joint_right_upper.stl would be clearer for the originals and MGN12x_MNG12y_joint_right_upper.stl for the MGN12 Y axis mod.

I reported the issue cause I didn't want someone else to make the same mistake as I did.

Closed 2025-04-14.

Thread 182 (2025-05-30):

current electronics bay design isn't compliant in Germany (and possibly elsewhere)

Nathan22211, 2025-05-30:
While I know this isn't required in the US and by the EU in general. Talking to Blackbird in Discord, who's German, brought up that their electrical codes require high voltage and low voltage electronics to be physically separated, i.e. on different faces of a machine.

I'd implore that an optional backpack mod is made if this is the case in a user's home region.

this also affects the 2.4, I don't think the V0 has anything considered high voltage and I know nothing of the switchwire or legacy to determine if they're affected as well.

nemgrea, 2025-05-30:
can you please cite the relevant code or provide a source that we can look over? this seems like a very simplified explanation and one that would present problems for a typical PSU as that in itself contains both mains and low DC voltage terminals. I find it hard to believe that youd have to bisect the PSU in order to "separate" high and low voltage....

we need more information here...

Nathan22211, 2025-05-30:
found this https://cms.law/en/int/expert-guides/cms-expert-guide-to-electricity/germany and this https://www.baua.de/EN/Topics/Work-design/Safe-products/Electrical-products/Requirements/Conformity

basic search query if you want to look into it further: https://www.bing.com/search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

blackbird is a electrician over there so he could give info as well

nemgrea, 2025-05-30:
these are both rather vague and not really answering the question of what specifically it is that is in violation....

you HAVE to run mains wiring from the AC parts to the PSU and the PSU HAS to have DC and AC terminals next to each other...

where is the violation occurring? what is the threshold for "High Voltage"? where is the "different faces of a machine" claim coming from?

BerzerkaDurk, 2025-06-19:
How are you defining the terms "high voltage" and "low voltage"?

To answer one of your questions, @nemgrea, in Germany, "High Voltage" is defined as voltages over 1,000VAC or 1,500VDC.
"Low Voltage" refers to 50VAC to 1,000VAC or 120VDC to 1,500VDC.
Voltages under 50VAC and 120VDC are referred to as "Extra-Low Voltage"

In any case, unless I'm mistaken, the regulations you are referencing only apply to devices bearing the CE designation.

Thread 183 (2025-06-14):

Manual: pg 231, M3x8 SHCS is too short

LumenMaintenance, 2025-06-14:
Trident Assembly Manual page 231 says to use an M3x8 SHCS to secure the wire cover. This is too short and does not thread into the heat set insert. An M3x12 SHCS is required.

Closed 2025-06-14.

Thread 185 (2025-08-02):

xy joint mislabel

Spinnertebug, 2025-08-02:
The xy joints found under the path(s)

STLs/Gantry/X_Axis/XY_Joints/xy_joint_left_lower_MGN12.stl
STLs/Gantry/X_Axis/XY_Joints/xy_joint_left_upper_MGN12.stl
STLs/Gantry/X_Axis/XY_Joints/xy_joint_right_lower_MGN12.stl
STLs/Gantry/X_Axis/XY_Joints/xy_joint_right_upper_MGN12.stl

Do not have the hole spacing for MGN12H or MGN12C, The github file tree name on this may be referring to the linear rail on the "x axis" linear rail itself, however this is misleading and may cause confusion among new builders.

shiftingtech, 2025-08-02:
There are no accommodations in the bom, the manual, or even any kit (that I'm aware of) for mgn12 y rails, whereas there are, historically, accommodations for a few different x axis configurations.  The file names are consistent with those things that actually exist within the voron ecosystem

shiftingtech, 2025-08-02:
Since this has been recently discussed in  #181 , I think there's no need for a further rehash.

Closed 2025-08-02.

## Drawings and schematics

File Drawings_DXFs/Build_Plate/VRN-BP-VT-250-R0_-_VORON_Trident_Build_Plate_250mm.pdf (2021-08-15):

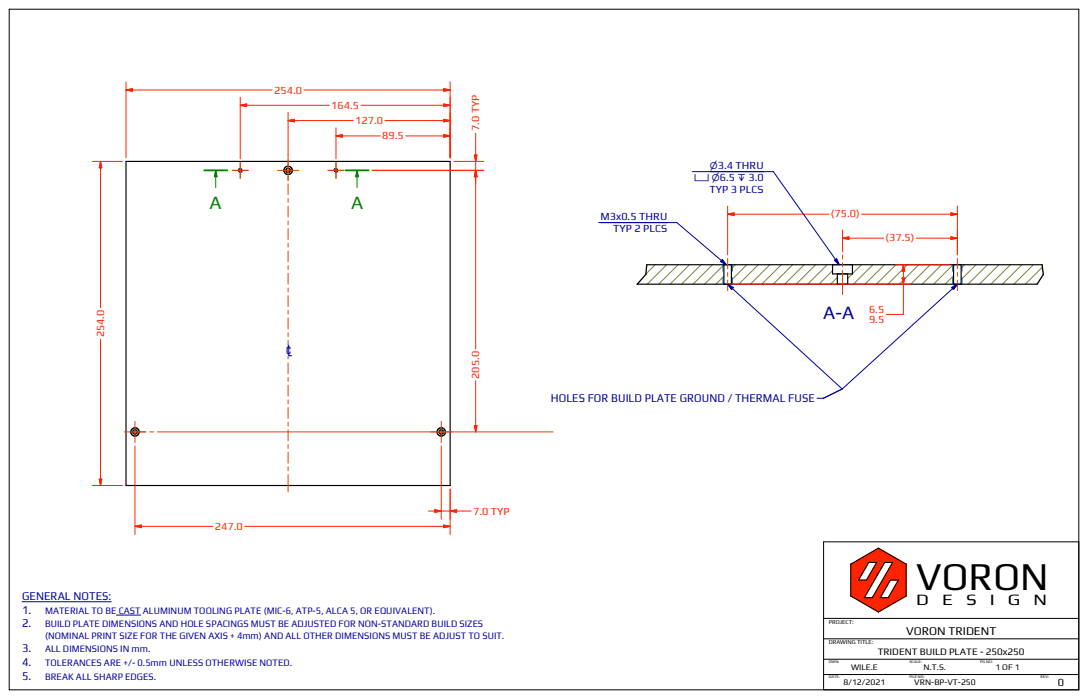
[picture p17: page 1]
VRN-BP-VT-250 DATE:; FILE NO:; PROJECT:; DRAWING TITLE:; VORON TRIDENT; TRIDENT BUILD PLATE - 250x250 DWN:; SCALE:; WILE.E; VORON; REV:; 7.0 TYP; M3x0.5 THRU TYP 2 PLCS; n3.4 THRU vn6.5 x 3.0 TYP 3 PLCS

HOLES FOR BUILD PLATE GROUND / THERMAL FUSE

GENERAL NOTES:
1. MATERIAL TO BE CAST ALUMINUM TOOLING PLATE (MIC-6, ATP-5, ALCA 5, OR EQUIVALENT).
2. BUILD PLATE DIMENSIONS AND HOLE SPACINGS MUST BE ADJUSTED FOR NON-STANDARD BUILD SIZES
(NOMINAL PRINT SIZE FOR THE GIVEN AXIS + 4mm) AND ALL OTHER DIMENSIONS MUST BE ADJUST TO SUIT.
3. ALL DIMENSIONS IN mm.
4. TOLERANCES ARE +/- 0.5mm UNLESS OTHERWISE NOTED.
5. BREAK ALL SHARP EDGES.

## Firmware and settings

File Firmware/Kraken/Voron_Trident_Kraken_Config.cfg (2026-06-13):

# This file contains common pin mappings for the BigTreeTech Kraken.
# To use this config, the firmware should be compiled for the STM32H723Z6 with a "128KiB bootloader"
# Enable "extra low-level configuration options" and select the "25MHz crystal" as clock reference

# after running "make", copy the generated "klipper/out/klipper.bin" file to a
# file named "firmware.bin" on an SD card and then restart the Kraken with that SD card.

# See docs/Config_Reference.md for a description of parameters.

## Voron Design VORON Trident 250/300/350mm BigTreeTech Kraken

## *** THINGS TO CHANGE/CHECK: ***
## MCU paths                            [mcu] section
## Thermistor types                     [extruder] and [heater_bed] sections - See https://www.klipper3d.org/Config_Reference.html#common-thermistors for common thermistor types
## Hotend heater pin                    [extruder] section
## Leadscrew Rotation Distance          [stepper_z], [stepper_z1], [stepper_z2]
## Z Endstop Switch location            [safe_z_home] section
## Z Endstop Switch  offset for Z0      [stepper_z] section
## Stepper Z1 enable pin                [stepper_z1] section
## PID tune                             [extruder] and [heater_bed] sections
## Probe pin                            [probe] section
## Fine tune E steps                    [extruder] section

[mcu]
##  Obtain definition by "ls /dev/serial/by-id/*" then unplug to verify
##--------------------------------------------------------------------
serial: /dev/serial/by-id/{REPLACE WITH YOUR SERIAL}
restart_method: command
##--------------------------------------------------------------------

[printer]
kinematics: corexy
max_velocity: 300  
max_accel: 3000             #Max 4000
max_z_velocity: 15          #Max 15 for 12V TMC Drivers, can increase for 24V
max_z_accel: 350
square_corner_velocity: 5.0

#####################################################################
#   X/Y Stepper Settings
#####################################################################

##  B Stepper - Left
##  Connected to Motor_1-S1
##  Endstop connected to MIN1
[stepper_x]
step_pin: PC14
dir_pin: !PC13
enable_pin: !PE6
rotation_distance: 40
microsteps: 32
full_steps_per_rotation:200  #set to 400 for 0.9 degree stepper
endstop_pin: PC15
position_min: 0
##--------------------------------------------------------------------

##  Uncomment below for 250mm build
#position_endstop: 250
#position_max: 250

##  Uncomment for 300mm build
#position_endstop: 300
#position_max: 300

##  Uncomment for 350mm build
#position_endstop: 350
#position_max: 350

##--------------------------------------------------------------------
homing_speed: 25   #Max 100
homing_retract_dist: 5
homing_positive_dir: true

##  TMC2160 configuration
[tmc5160 stepper_x]
cs_pin: PD6
interpolate: false
spi_software_miso_pin: PC7
spi_software_mosi_pin: PC8
spi_software_sclk_pin: PC6
sense_resistor: 0.022
run_current: 0.800
stealthchop_threshold: 0
##  sensorless homing, plug in jumper on M2-DIAG
#diag1_pin: PC15

##  A Stepper - Right
##  Connected to Motor_2-S2
##  Endstop connected to MIN2
[stepper_y]
step_pin: PE5
dir_pin: !PE4
enable_pin: !PE3
rotation_distance: 40
microsteps: 32
full_steps_per_rotation:200  #set to 400 for 0.9 degree stepper
endstop_pin: PF0
position_min: 0
##--------------------------------------------------------------------

##  Uncomment for 250mm build
#position_endstop: 250
#position_max: 250

##  Uncomment for 300mm build
#position_endstop: 300
#position_max: 300

##  Uncomment for 350mm build
#position_endstop: 350
#position_max: 350

##--------------------------------------------------------------------
homing_speed: 25  #Max 100
homing_retract_dist: 5
homing_positive_dir: true

##  TMC2160 configuration
[tmc5160 stepper_y]
cs_pin: PD5
interpolate: false
spi_software_miso_pin: PC7
spi_software_mosi_pin: PC8
spi_software_sclk_pin: PC6
sense_resistor: 0.022
run_current: 0.800
stealthchop_threshold: 0
##  sensorless homing, plug in jumper on M2-DIAG
#diag1_pin: PF0
 
#####################################################################
#   Z Stepper Settings
#####################################################################

## Z0 Stepper - Front Left
##  Connected to Motor_5-S5
##  Endstop connected to MIN3
[stepper_z]
step_pin: PG9
dir_pin: PG10
enable_pin: !PG13
# Rotation Distance for TR8x8 = 8, TR8x4 = 4, TR8x2 = 2
# rotation_distance: 8    
microsteps: 32
endstop_pin: PF1
##  Z-position of nozzle (in mm) to z-endstop trigger point relative to print surface (Z0)
##  (+) value = endstop above Z0, (-) value = endstop below
##  Increasing position_endstop brings nozzle closer to the bed
##  After you run Z_ENDSTOP_CALIBRATE, position_endstop will be stored at the very end of your config
position_endstop: -0.5
## All builds use same Max Z
position_max: 250
position_min: -2.5
homing_speed: 8.0 # Leadscrews are slower than 2.4, 10 is a recommended max.
second_homing_speed: 3
homing_retract_dist: 3

##  TMC2160 configuration
[tmc5160 stepper_z]
cs_pin: PD2
interpolate: false
spi_software_miso_pin: PC7
spi_software_mosi_pin: PC8
spi_software_sclk_pin: PC6
sense_resistor: 0.075
run_current: 0.800
stealthchop_threshold: 0

##  Z1 Stepper - Rear Center
##  Connected to Motor_6-S6
[stepper_z1]
step_pin: PG11
dir_pin: PD7
enable_pin: !PG12
# Rotation Distance for TR8x8 = 8, TR8x4 = 4, TR8x2 = 2
# rotation_distance: 8  
microsteps: 32

##  TMC2160 configuration
[tmc5160 stepper_z1]
cs_pin: PA15
interpolate: false
spi_software_miso_pin: PC7
spi_software_mosi_pin: PC8
spi_software_sclk_pin: PC6
sense_resistor: 0.075
run_current: 0.800
stealthchop_threshold: 0

##  Z2 Stepper - Front Right
##  Connected to Motor_7-S7
[stepper_z2]
step_pin: PB4
dir_pin: PB3
enable_pin: !PB5
# Rotation Distance for TR8x8 = 8, TR8x4 = 4, TR8x2 = 2
# rotation_distance: 8  
microsteps: 32

##  TMC2160 configuration
[tmc5160 stepper_z2]
cs_pin: PA9
interpolate: false
spi_software_miso_pin: PC7
spi_software_mosi_pin: PC8
spi_software_sclk_pin: PC6
sense_resistor: 0.075
run_current: 0.800
stealthchop_threshold: 0


#####################################################################
#   Extruder
#####################################################################

##  Connected to MOTOR_3-S3
##  Heater - HE0
##  Thermistor - TH0
[extruder]
step_pin: PE2
dir_pin: PE1
enable_pin: !PE0
##  Update value below when you perform extruder calibration
##  If you ask for 100mm of filament, but in reality it is 98mm:
##  rotation_distance = <previous_rotation_distance> * <actual_extrude_distance> / 100
##  22.6789511 is a good starting point
rotation_distance: 22.6789511   #Bondtech 5mm Drive Gears
##  Update Gear Ratio depending on your Extruder Type
##  Use 50:10 for Stealthburner/Clockwork 2
##  Use 50:17 for Afterburner/Clockwork (BMG Gear Ratio)
##  Use 80:20 for M4, M3.1
gear_ratio: 50:10
microsteps: 32
full_steps_per_rotation: 200    #200 for 1.8 degree, 400 for 0.9 degree
nozzle_diameter: 0.400
filament_diameter: 1.75
heater_pin: PF6
## Check what thermistor type you have. See https://www.klipper3d.org/Config_Reference.html#common-thermistors for common thermistor types.
## Use "Generic 3950" for NTC 100k 3950 thermistors
#sensor_type:
sensor_pin: PB1
min_temp: 10
max_temp: 270
max_power: 1.0
min_extrude_temp: 170
control = pid
pid_kp = 26.213
pid_ki = 1.304
pid_kd = 131.721
##  Try to keep pressure_advance below 1.0
#pressure_advance: 0.05
##  Default is 0.040, leave stock
#pressure_advance_smooth_time: 0.040

##  E0 on MOTOR_3-S3
##  TMC2160 configuration
[tmc5160 extruder]
cs_pin: PD4
interpolate: false
spi_software_miso_pin: PC7
spi_software_mosi_pin: PC8
spi_software_sclk_pin: PC6
sense_resistor: 0.022
run_current: 0.500
stealthchop_threshold: 0


#####################################################################
#   Bed Heater
#####################################################################

##  SSR Pin - HE1
##  Thermistor - THB
[heater_bed]
##  Uncomment the following line if using the default SSR wiring from the docs site
#heater_pin: PF7
##  Other wiring guides may use BED_OUT to control the SSR. Uncomment the following line for those cases
#heater_pin: PF5
## Check what thermistor type you have. See https://www.klipper3d.org/Config_Reference.html#common-thermistors for common thermistor types.
## Use "Generic 3950" for Keenovo heaters
#sensor_type:
sensor_pin: PB0
##  Adjust max_power so it doesn't exceed the SSR rating. The Omron G3NA-210B-DC5 SSR is rated at 4 amps without a heatsink.
##  The formula is "4 / (Wattage_of_bed_heater / Mains_voltage) = max_power"
##  If max_power is greater than 1.0, use 1.0
max_power: 0.6
min_temp: 0
max_temp: 120
control: pid
pid_kp: 58.437
pid_ki: 2.347
pid_kd: 363.769

#####################################################################
#   Probe
#####################################################################
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

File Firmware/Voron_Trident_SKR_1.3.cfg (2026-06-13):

## *** THINGS TO CHANGE/CHECK: ***
## MCU paths                             [mcu] section
## Thermistor types                      [extruder] and [heater_bed] sections - See https://www.klipper3d.org/Config_Reference.html#common-thermistors for common thermistor types
## Z Endstop Switch location             [homing_override] section
## Z Endstop Switch  offset for Z0       [stepper_z] section
## PID tune                              [extruder] and [heater_bed] sections
## Fine tune E steps                     [extruder] section

##========================== Pin Definitions ========================
## X_STEP_PIN         2.2
## X_DIR_PIN          2.6
## X_ENABLE_PIN       2.1
## X_MIN_PIN          1.29
## X_MAX_PIN          1.28
## X_UART_RX          1.17
## X_UART_TX          4.29

## Y_STEP_PIN         0.19
## Y_DIR_PIN          0.20
## Y_ENABLE_PIN       2.8
## Y_MIN_PIN          1.27
## Y_MAX_PIN          1.26
## Y_UART_RX          1.15
## Y_UART_TX          1.16

## Z_STEP_PIN         0.22
## Z_DIR_PIN          2.11
## Z_ENABLE_PIN       0.21
## Z_MIN_PIN          1.25
## Z_MAX_PIN          1.24
## Z_UART_RX          1.10
## Z_UART_TX          1.14

## E0_STEP_PIN        2.13
## E0_DIR_PIN         0.11
## E0_ENABLE_PIN      2.12
## E0_UART_RX         1.8
## E0_UART_TX         1.9

## E1_STEP_PIN        0.1
## E1_DIR_PIN         0.0
## E1_ENABLE_PIN      0.10
## E1_UART_RX         1.1
## E1_UART_TX         1.4

## HE1                2.4    
## HE0                2.7
## BED                2.5
## TH1 (H1 Temp)      0.25
## TH0 (H0 Temp)      0.24jj
## TB  (Bed Temp)     0.23
## FAN                2.3
## SERVO              2.0
##===================================================================

#Mainsail support
[pause_resume]
[display_status]


[virtual_sdcard]
path: ~/gcode_files


[printer]
kinematics: corexy
max_velocity: 300  
max_accel: 3000
max_z_velocity: 5
max_z_accel: 100
square_corner_velocity: 5.0  

[mcu]
###Change to device found by "ls /dev/serial/by-id/*" with just one this MCU connected to Pi
serial: /dev/serial/by-id/usb-Klipper_lpc1768_XXXXXXXXXXXXXXXXXXXXX

###Change to device found by "ls /dev/serial/by-id/*" with just one this MCU connected to Pi
[mcu xye]
serial: /dev/serial/by-id/usb-Klipper_lpc1768_XXXXXXXXXXXXXXXXXXXXX



#####################################################################
#   X/Y Stepper Settings
#####################################################################

######
#X motor slot on XYE board (B Motor)
###############
[stepper_x]
# X_STEP_PIN         2.2
# X_DIR_PIN          2.6
# X_ENABLE_PIN       2.1
# X_MIN_PIN          1.29
# X_MAX_PIN          1.28
# X_UART_RX          1.17
# X_UART_TX          4.29
step_pin: xye:P2.2
dir_pin: !xye:P2.6
enable_pin: !xye:P2.1
#step_distance: 0.0125
rotation_distance: 40
microsteps: 16
full_steps_per_rotation: 200
## X+ Endstop on XYE board
endstop_pin: xye:P1.28
position_min: 0

##  Uncomment below for 250mm build
#position_endstop: 250
#position_max: 250

##  Uncomment for 300mm build
#position_endstop: 300
#position_max: 300

##  Uncomment for 350mm build
#position_endstop: 350
#position_max: 350

##--------------------------------------------------------------------
homing_speed: 25   #Max 100
homing_retract_dist: 5
homing_positive_dir: true

##  Make sure to update below for your relevant driver (2208 or 2209)
[tmc2209 stepper_x]
uart_pin: xye:P1.17
interpolate: True
run_current: 0.8
hold_current: 0.7
sense_resistor: 0.110
stealthchop_threshold: 0

######
#Y motor slot on XYE board (A Motor)
###############
[stepper_y]
# Y_STEP_PIN         0.19
# Y_DIR_PIN          0.20
# Y_ENABLE_PIN       2.8
# Y_MIN_PIN          1.27
# Y_MAX_PIN          1.26
# Y_UART_RX          1.15
# Y_UART_TX          1.16
step_pin: xye:P0.19
dir_pin: !xye:P0.20
enable_pin: !xye:P2.8
rotation_distance: 40
full_steps_per_rotation: 200
microsteps: 16
# Y+ Endstop on XYE board
endstop_pin: xye:P1.26
position_min: 0
##--------------------------------------------------------------------
##  Uncomment for 250mm build
#position_endstop: 250
#position_max: 250

##  Uncomment for 300mm build
#position_endstop: 300
#position_max: 300

##  Uncomment for 350mm build
#position_endstop: 350
#position_max: 350
##--------------------------------------------------------------------
homing_speed: 25  #Max 100
homing_retract_dist: 5
homing_positive_dir: true

##  Make sure to update below for your relevant driver
[tmc2209 stepper_y]
uart_pin: xye:P1.15
interpolate: True
run_current: 0.8
hold_current: 0.7
sense_resistor: 0.110
stealthchop_threshold: 0

#####################################################################
#   Z Stepper Settings
#####################################################################

######
# Z0 Stepper - Left Front
# E1 Motor Slot on Z(main) board
###############
[stepper_z]
# E1_STEP_PIN        0.1
# E1_DIR_PIN         0.0
# E1_ENABLE_PIN      0.10
# E1_UART_RX         1.1
# E1_UART_TX         1.4
step_pin: P0.1
dir_pin: !P0.0
enable_pin: !P0.10
##T8x4 Lead Screws.  One rotation moves the bed 4mm 
##Change according to integrated steppers purchased
rotation_distance: 4
full_steps_per_rotation: 200
microsteps: 16
# Z Max Connector on Z(main) Board
endstop_pin: P1.25 
#  Z-position of nozzle (in mm) to z-endstop trigger point relative to print surface (Z0)
#  (+) value = endstop above Z0, (-) value = endstop below
#  Increasing position_endstop brings nozzle closer to the bed
#  After you run Z_ENDSTOP_CALIBRATE, position_endstop will be stored at the very end of your config
position_endstop: -0.5
## All builds use same Max Z
position_max: 250

##--------------------------------------------------------------------
position_min: -5
homing_speed: 8 # Leadscrews are slower than 2.4, 10 is a recommended max.
second_homing_speed: 3.0
homing_retract_dist: 3.0

##  Make sure to update below for your relevant driver (2208 or 2209)
[tmc2209 stepper_z]
uart_pin: P1.1
interpolate: true
run_current: 0.6
hold_current: 0.6
sense_resistor: 0.110
stealthchop_threshold: 0

######
#Z Stepper - Rear Center
#Z Motor Slot on Z(main) board
###############
[stepper_z1]
## Z_STEP_PIN         0.22
## Z_DIR_PIN          2.11
## Z_ENABLE_PIN       0.21
## Z_UART_RX          1.10
## Z_UART_TX          1.14
step_pin: P0.22
dir_pin: !P2.11
enable_pin: !P0.21
##T8x4 Lead Screws.  One rotation moves the bed 4mm 
##Change according to integrated steppers purchased
rotation_distance: 4
full_steps_per_rotation: 200
microsteps: 16


##  Make sure to update below for your relevant driver (2208 or 2209)
[tmc2209 stepper_z1]
uart_pin: P1.10
interpolate: true
run_current: 0.6
hold_current: 0.6
sense_resistor: 0.110
stealthchop_threshold: 0

##  Main MCU - In X Position
##  Z2 Stepper - Front Right

######
#Z Stepper - Front Right
#X Motor Slot on Z(main) board
###############
[stepper_z2]
## X_STEP_PIN         2.2
## X_DIR_PIN          2.6
## X_ENABLE_PIN       2.1
## X_UART_RX          1.17
## X_UART_TX          4.29
step_pin: P2.2
dir_pin: !P2.6
enable_pin: !P2.1
## T8x4 Lead Screws.  One rotation moves the bed 4mm 
## Change according to integrated steppers purchased
rotation_distance: 4
full_steps_per_rotation: 200
microsteps: 16

##  Make sure to update below for your relevant driver (2208 or 2209)
[tmc2209 stepper_z2]
uart_pin: P1.17
interpolate: True
run_current: 0.6
hold_current: 0.6
sense_resistor: 0.110
stealthchop_threshold: 0

######
#Extruder 0 slot on XYE board
###############
[extruder]
# E0_STEP_PIN        2.13
# E0_DIR_PIN         0.11
# E0_ENABLE_PIN      2.12
# E0_UART_RX         1.8
# E0_UART_TX         1.9
step_pin: xye:P2.13
dir_pin: xye:P0.11
enable_pin: !xye:P2.12
##  Update value below when you perform extruder calibration
##  If you ask for 100mm of filament, but in reality it is 98mm:
##  rotation_distance = <previous_rotation_distance> * <actual_extrude_distance> / 100
##  22.6789511 is a good starting point
rotation_distance: 22.6789511   #Bondtech 5mm Drive Gears
##  Update Gear Ratio depending on your Extruder Type
##  Use 50:10 for Stealthburner/Clockwork 2
##  Use 50:17 for Afterburner/Clockwork (BMG Gear Ratio)
##  Use 80:20 for M4, M3.1
gear_ratio: 50:10
microsteps: 16
full_steps_per_rotation: 200
nozzle_diameter: 0.400
filament_diameter: 1.75
heater_pin: xye:P2.7
## Check what thermistor type you have. See https://www.klipper3d.org/Config_Reference.html#common-thermistors for common thermistor types.
## Use "Generic 3950" for NTC 100k 3950 thermistors
#sensor_type:
sensor_pin: xye:P0.24
min_temp: 10
max_temp: 270
max_power: 1.0
min_extrude_temp: 170
control = pid
pid_kp = 26.213
pid_ki = 1.304
pid_kd = 131.721
#Set appropriate once tuning your printer
#pressure_advance: .05
##  Default is 0.040, leave stock
pressure_advance_smooth_time: 0.040
max_extrude_only_distance: 200.0

##  Make sure to update below for your relevant driver
[tmc2209 extruder]
uart_pin: xye:P1.8
run_current: 0.5
hold_current: 0.4
sense_resistor: 0.110
stealthchop_threshold: 0
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

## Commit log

2021-08-15 Initial files
    [10mm_extrusion_drill_guide.stl, 110mm_Y_alignment_spacer_x2.stl, 140mm_extrusion_drill_guide.stl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]
2021-08-15 Fix BMO filenames
    [printhead_front_dragonfly_bmo.stl, printhead_rear_dragonfly_bmo.stl]
2021-08-15 fix quantity.
    [pcb_din_clip_v2.stl]
2021-08-16 Rename Assembly Manual, Remove Steve's SKR1.4 Config
    [SKR14T_EXPMOT.cfg]
2021-08-16 Add PCB Din Clip
    [pcb_din_clip_v2_x5.stl]
2021-08-16 Fix Controller mount filenames
    [Duet2_Duet3Mini5_bracket_x2.stl, GTR_bracket_x2.stl, Octopus_bracket_x2.stl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]
2021-08-16 Revert "Fix Controller mount filenames"
    This reverts commit 1ac235fffacc616b603173ee455464d03bf448e5.
    [Duet2_Duet3Mini5_bracket_2pc.stl, GTR_bracket_2pc.stl, Octopus_bracket_2pc.stl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]
2021-08-16 Update CAD filenames
2021-08-16 manual updates (#6)
    Assembly Manual
    page 12 - updated drawing, single tapped end
    page 16 - fixed typo
    page 50 - fixed typo
    page 56 - fixed typo
    page 57 - added instructions
    page 90 - fixed typo
    page 117 - fixed M3x216 callout
    page 121 - spelling
    page 124 - spelling
    page 134 - typo
    page 136 - typo
    page 166 - typo
    page 182 - added spacing callout
    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
2021-08-21 Updated position of the M5 hex nuts for better thread engagement. Minor change, no reprint necessary.
    [z_carriage_left.stl, z_carriage_rear_2hole.stl, z_carriage_rear_3hole.stl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]
2021-08-21 Corrected issue with the Mini12864 display housing that was preventing the encoder knob from fully engaging when pressed.
    [[a]_mini12864_case_front_insert.stl, mini12864_case_front.stl, mini12864_case_rear.stl]
2021-08-21 Updated CAD assembly files with changes contained in pr_vt_210821
2021-08-23 Fix z tilt coordinates.
    [Voron_Trident_SKR14_EXPMOT.cfg, Voron_Trident_SKR_1.3.cfg]
2021-08-30 Manual Update (#13)
    Assembly_Manual_Trident
    page 132 - corrected extrusion callout
    page 195 - changed screw callout to reflect updated model
    various pages: spelling
    Frame_Upgrade_Trident
    page 8 - updated instructions
2021-08-31 Included updated blower_housing_rear.stl from the AB repo. Exported probe_retainer_bracket_9mm.stl for Panasonic probes. Updated CAD assemblies to reflect the blower housing change.
    [blower_housing_rear.stl, probe_retainer_bracket_9mm.stl]
2021-08-31 Removed a couple of redundant sections in Voron_Trident_SKR14_EXPMOT.cfg.
    [Voron_Trident_SKR14_EXPMOT.cfg]
2021-09-19 Homing override fixes (#16)
    * Update Voron_Trident_SKR14_EXPMOT.cfg
    Update homing_override default position to -10,-10 to cause error when not updated properly.
    * Update Voron_Trident_SKR_1.3.cfg
    Update homing_override default position to -10,-10 to cause error when not updated properly.
    * Update Voron_Trident_SKR14_EXPMOT.cfg
    Comment Change
    * Update Voron_Trident_SKR_1.3.cfg
    Comment Change
    [Voron_Trident_SKR14_EXPMOT.cfg, Voron_Trident_SKR_1.3.cfg]
2021-11-01 fix: correct z_tilt z_positions (#19)
    [Voron_Trident_SKR14_EXPMOT.cfg, Voron_Trident_SKR_1.3.cfg]
2021-12-15 Update Assembly_Manual_Trident.pdf
    Closes #38
    Closes #36
    Closes #35
    Closes #33
    Closes #30
    Closes #27
    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
2021-12-28 Octopus config for Trident (#32)
    * Add klipper config for BTT Octopus
    * Remove duplicate microsteps value. require user to configure rotation distance. update thermistor types.
    * Updates from feedback. Reduced Z motor current. Removed QGL and replaced with z_tilt. Comment out PA values.
    * Comment out all z_tilt options to require user choice.
    * remove hold_current values, as hold_current defaults to run_current.
    [Trident_Octopus_Config.cfg]
2021-12-30 Remove leading spaces from selectable config options (#44)
    * Remove references to quad gantry leveling from config files.
    * Remove spaces from selectable config options
    [Trident_Octopus_Config.cfg, Voron_Trident_SKR14_EXPMOT.cfg, Voron_Trident_SKR_1.3.cfg]
2022-01-21 Updated Mini12864 rear case and added an encoder knob light shield to better fit BigTreeTech variant of the display. (#50)
    [[a]_btt_knob_light_shield.stl, mini12864_case_rear.stl]
2022-01-22 Update Trident_Octopus_Config.cfg (#51)
    Fix Z2 direction
    [Trident_Octopus_Config.cfg]
2022-01-26 Adding Fysetc controller mount STLs BIGDIPPER_bracket_2pc.stl and S6_bracket_2pc.stl. (#52)
    [BIGDIPPER_bracket_2pc.stl, S6_bracket_2pc.stl]
2022-02-12 Update Assembly_Manual_Trident.pdf (#55)
    Page 18 - Added reference to other frame sizes
    Page 53 - Added graphics to clarify back brace
    Page 54 - Added reference to other frame sizes
    Page 118 - Updated instructions
    Page 127 - Added graphics to clarify orientation
    Page 127 - Added labels for orientation
    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
2022-04-30 Remove default sensor_types, convert tabs to spaces (#67)
    * Remove default sensor_types
    * Comment out sensor_types, convert tabs to spaces
    * Remove 3950 footnotes, ensure newlines at end of configs
    [Trident_Octopus_Config.cfg, Voron_Trident_SKR14_EXPMOT.cfg, Voron_Trident_SKR_1.3.cfg]
2022-05-19 Voron Trident r1 Updates (#68)
    * Revised front idlers with tensioning screws moved to be inline with the idler pulleys. Inspiration for this modification taken from Github issue posted by chrisingham05
    * Correct misplaced heatset insert on front_skirt_a_350.stl. Fixes issue #62.
    * Added space for Spider V2.2 under-board fuse (Fixes issue #57). Renamed all applicable controllers from _2pc.stl to _set.stl
    * Modified XY joints and AB drive units unsupported countersunk bolt holes with the cross-bridge method. (Fixes issue #22).
    * Copied all applicable changes from Voron Afterburner PR's 120 and 121.
    * Changed all panel components with cross-bridge countersunk hole method. Rena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
    [AB_pulley_jig.stl, BIGDIPPER_bracket_set.stl, Duet2_Duet3Mini5_bracket_set.stl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]
2022-12-13 Added Gear Ratio for CW2 to printer.cfg (#84)
    * Added Gear Ratio for CW2
    * Added Gear Ratio for CW2
    [Trident_Octopus_Config.cfg]
2023-01-03 Add Frame_Upgrade_Trident.pdf (#90)
    Restores the frame upgrade manual before r1 release.
2023-03-01 Stl size fix (#101)
    * Delete a_drive_frame_lower.stl
    * Delete b_drive_frame_lower.stl
    * Add files via upload
2023-06-26 Update Voron_Trident_SKR14_EXPMOT.cfg (#123)
    removed spurious pressure advance values
    [Voron_Trident_SKR14_EXPMOT.cfg]
2023-07-18 stealthburner integration (#124)
    * SB
    * Update README.md
    * Update README.md
    * Update README.md
    * Create readme.md
    * Update readme.md
    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
    [Trident_Octopus_Config.cfg, Voron_Trident_SKR14_EXPMOT.cfg, Voron_Trident_SKR_1.3.cfg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]
2023-08-08 Added тαкυуα's M8P 1.0 config (#116)
    [Trident_M8P_config.cfg]
2023-09-07 updated trident assembly to included fixed CW2 chain anchor and remove the SW chain anchors that were there also aligned the chain properly to the mount as well (#128)
2023-09-09 Update config files to reflect SSR rating instead of the old, incorrect "warp" rating. (#130)
    Change bed_heater formula to insure max_power doesn't exceed SSR rating.
    Change bed_heater formula to insure max_power doesn't exceed SSR rating.
    * Update Trident_M8P_config.cfg
    Change bed_heater formula to insure max_power doesn't exceed SSR rating.
    * Update Trident_Octopus_Config.cfg
    Change bed_heater formula to insure max_power doesn't exceed SSR rating.
    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
    [Trident_M8P_config.cfg, Trident_Octopus_Config.cfg, Voron_Trident_SKR14_EXPMOT.cfg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]
2023-10-29 octopus pro 1.1 config changes (#137)
    [Trident_Octopus_Config.cfg]
2023-11-07 Fix config file consistency and clarify GCode state command usage (#136)
    The PRINT_END macro in the Octopus config file contains a pair of
    SAVE_GCODE_STATE/RESTORE_GCODE_STATE command. The purpose of those
    commands is to allow the macro to perfom actions at the end of the
    print and then restore the printer state as it was prior to the
    macro's execution (restore coordinate system and speeds).
    However, there was some confusion as to the effect of those calls,
    particularly the RESTORE_GCODE_STATE. What is desired is that the
    printer state is restored but the toolhead position is not.
    To clarify the intention and prevent any issues, the "MOVE=0"
    argument to RESTORE_GCODE_STATE is ad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
    [Trident_M8P_config.cfg, Trident_Octopus_Config.cfg, Voron_Trident_SKR14_EXPMOT.cfg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]
2023-12-03 updated XY joint STLs to use hole bridging (#141)
    [xy_joint_left_lower_MGN12.stl, xy_joint_left_upper_MGN12.stl, xy_joint_right_lower_MGN12.stl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]
2023-12-03 Revert "updated XY joint STLs to use hole bridging (#141)" (#142)
    This reverts commit ef30e556cb023a9756f0934bcdfffbf824a7e153.
    [xy_joint_left_lower_MGN12.stl, xy_joint_left_upper_MGN12.stl, xy_joint_right_lower_MGN12.stl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]
2023-12-18 updated CAD assembly for trident (#143)
    * updated CAD assembly for trident
    * updated the CAD assembly
2024-01-02 [BUGFIX] Use Z_TILT_ADJUST for bed leveling (#148)
    The config is using QGL in the G32 macro even though it's for a Trident.
    [Trident_M8P_config.cfg]
2024-02-29 Voron Trident Kraken Config (#155)
    * Create Voron_Trident_Kraken_Config.cfg
    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
    [Voron_Trident_Kraken_Config.cfg]
2024-06-10 Update Voron_Trident_Kraken_Config.cfg (#164)
    [Voron_Trident_Kraken_Config.cfg]
2024-07-14 config file cleanups (#168)
    * bringing Trident inline with recent config tweaks to Voron 2
    * "ls /dev/serial/by-id/*"
    [Trident_M8P_v1.0_config.cfg, Trident_M8P_v1.1_config.cfg, Trident_M8P_v2.0_config.cfg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]
2024-10-03 Trident_M8P_v2.0_config.cfg oops (#170)
    [Trident_M8P_v2.0_config.cfg]
2024-10-05 Update Trident_M8P_v2.0_config.cfg (#171)
    As per PR to voron-2 repo- correct some minor issues in m8p v2 config example
    [Trident_M8P_v2.0_config.cfg]
2024-11-20 Spelling fix (#174)
    * Delete STLs/Spool_Management/bowen_retainer.stl
    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
    [bowden_retainer.stl]
2025-01-23 Trident m8p cfg fix (#176)
    * Update Trident_M8P_v1.0_config.cfg
    * Update Trident_M8P_v1.1_config.cfg
    * Update Trident_M8P_v2.0_config.cfg
    [Trident_M8P_v1.0_config.cfg, Trident_M8P_v1.1_config.cfg, Trident_M8P_v2.0_config.cfg]
2025-06-15 updated cable cover to fix #91 (#184)
    [[a]_wire_cover.stl]
2026-05-31 Minor config fixes (#194)
    * fix: remove duplicate position_max in skr14 stepper_z
    * fix: un-invert stepper_z2 step_pin polarity on skr13
    * fix: complete truncated exhaust_fan pin to PA3 on kraken
    [Voron_Trident_Kraken_Config.cfg, Voron_Trident_SKR14_EXPMOT.cfg, Voron_Trident_SKR_1.3.cfg]
2026-06-13 Trident R2 release. (#195)
    [110mm_Y_alignment_spacer_x2.stl, 110mm_y_alignment_spacer.f3d, 250_deck.dxf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]
2026-06-13 Trident R2 firware updates and cleanup. (#196)
    [Trident_M8P_v1.0_config.cfg, Trident_M8P_v1.1_config.cfg, Trident_M8P_v2.0_config.cfg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]
2026-06-25 Trident R2 post release issue updates (#207)
    * Updated z_carriage_rear. Fixes issue #204
    * Updated [a]_xy_right.stl. Fixes issue #201.
    * Updated manual. Fixes issues #197, #200, and #202.
    * Added missing spool holder base native cad.
    ---------
    [[a]_xy_right.stl, [a]_z_carriage_rear.stl, spool_holder_base.f3d]
2026-06-25 docs: Add README for horizontal chain umbilical (#208)
2026-06-27 Removed 4mm panel clips, updated quantity for 6mm clips, updated assembly manual. Fixes issue #209. (#210)
    [corner_panel_clip_4mm_x8.stl, corner_panel_clip_6mm_x16.stl, midspan_panel_clip_4mm_x7.stl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]
